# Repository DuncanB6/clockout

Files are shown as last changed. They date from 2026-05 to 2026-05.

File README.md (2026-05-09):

# Clockout

For years, analog clocks have been wasting time. Toiling away 24/7, they're only really appreciated for their hard work a few seconds a day when somebody is finally able to spare a brief glance. Sounds horribly inefficient? It is. Luckily, there's Clockout. Clockout is an analog clock that only updates to the current time when somebody looks at it. Now you may ask, is this really more energy efficient? Thanks to the near constant processing to look for people, no. But is it cheaper than a regular clock? Not at all, it uses over $100 in components. However, does it perform better than a regular clock? Definitely not, although it does do decently well. For all its weaknesses, it blows away its competition in only one field. It's slightly funny.

When a user walks into the room in front of the clock, an IR motion detector recognizes their movement. This is sent to a Raspberry Pi, and a blue LED illuminates to let the user know they're seen. The Pi then uses a Pi Camera to try and pick out a face. If this is successful, another indicator LED lights up before the hands adjust. The Pi pulls the real time (internet connected) and adjusts the hands to that time using a stepper motor connected to a gearbox. The entire system is powered off of a laptop power supply, which is stepped down to 5V for the Pi. 12V is pulled off this buck board for the stepper. 

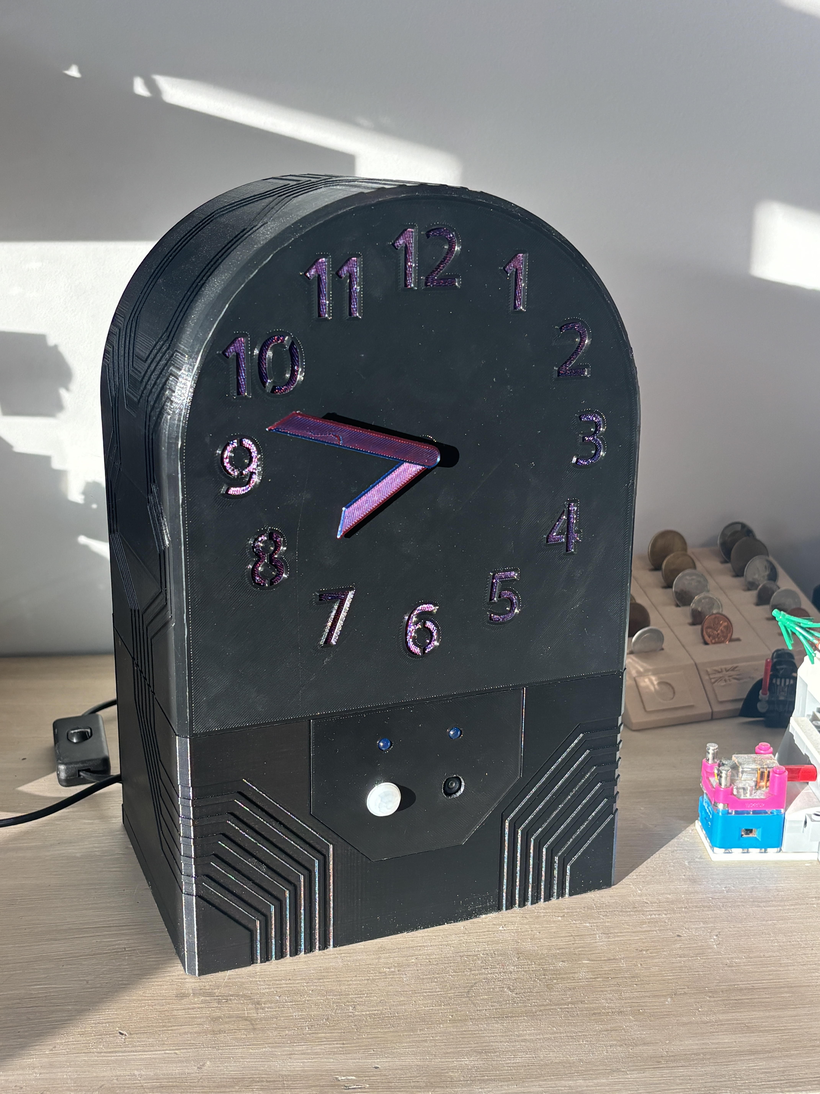
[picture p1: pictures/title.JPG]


This repository contains the software and hardware specs (STLs, BoM) that I used to make this project. Note that this is not a reproduction friendly project. You're welcome to use this idea, or even some of the resources here, but know that there are probably better options/designs out there.

## Software

Software for this project is a series of Python scripts. When running the primary script for full operation, functions from each script are used. Each individual script has a nameguarded section useful for testing it independantly.

### main.py

The main running file. This script handles all of the peripheral scripts, as well as handles the "state machine" and the hand adjustment math. 

#### Running the script
To run this script, use the following command:
"nohup python3 main.py 0630"

This runs the script indefinitely, even after disconnecting SSH. The argument (0630 in this case) should be the position of the clock hands when you run the script (6:30). See "calibrate.py" for positioning. To end the script, use the following two commands:
"ps aux | grep main.py"
"kill 4204"

Replace 4204 with the process ID discovered by the first command.

#### State machine

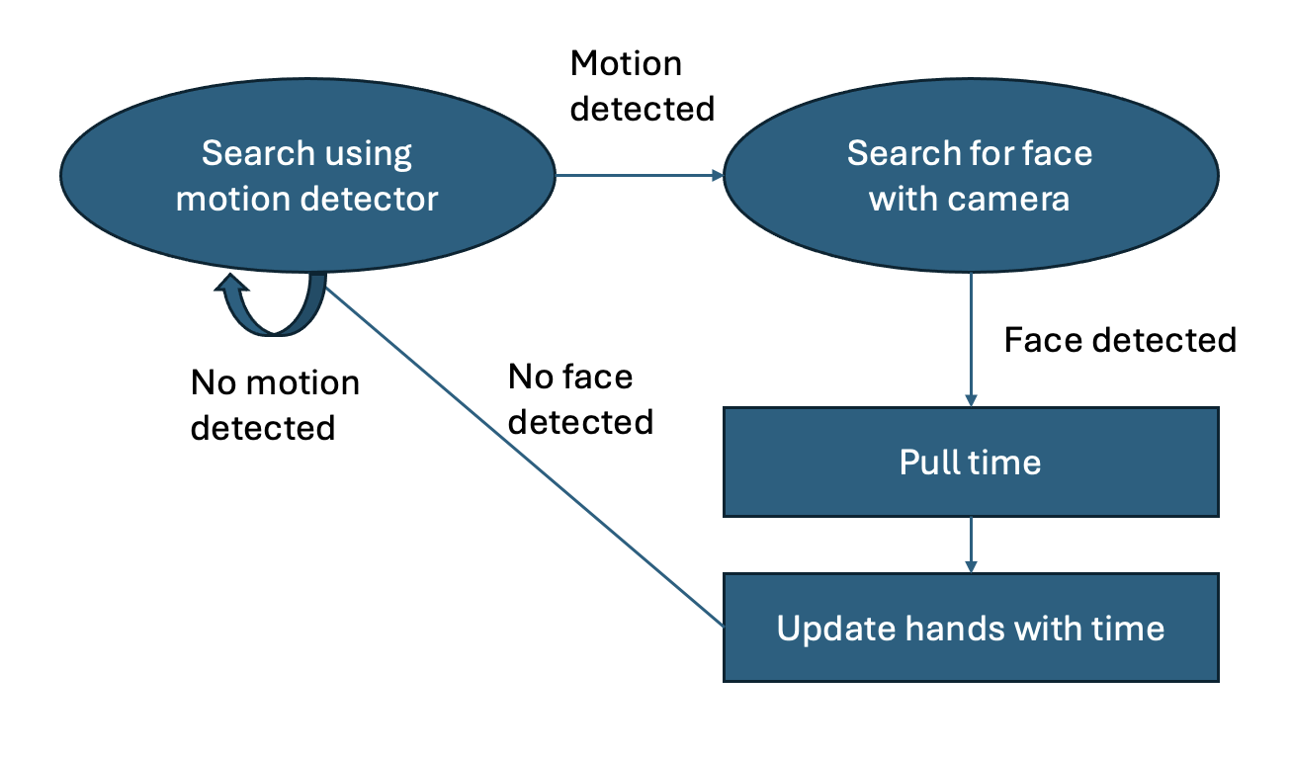
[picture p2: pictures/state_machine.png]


#### Clock hands math

This was one of the most technically challenging parts of the project surprisingly. It isn't all that complicated, but is hard to wrap your head around and hard to test (real time). This code finds the shortest distance in degrees between the current hands position and the desired position, then moves there.

### calibrate.py

This script allows the user to adjust the position of the hands. Enter a 4 digit number to exit. This is useful for testing, or if you'd like to line up the hands with a round time before starting for accuracy.

### camera.py

This script interacts with a Raspberry Pi PiCamera3 Wide Angle camera. It can take pictures, and detect faces in those pictures. Detection is done using a Haar cascade. A face is only registered when looking directly at the camera. Some tuning intructions are available in the comments. 

Watch out for the autofocus on this camera, if anything touches the lense area, it can mechanically block the autofocus, which causes problems for face detection.

### led.py

Dead simple script for toggling LEDs. Essentially a wrapper. 

### motion_detector.py

While this motion detector should probably be read using an ADC, it works pretty well as a digital read. This script simply takes that read.

### stepper.py

Controls the NEMA style stepper motor which spins the clock hands.

## Hardware

This section includes the component choices used in this project and the design of 3D printed components to house everything.

### BoM

See the BoM (excel sheet) in this repository. Note that the components used here are extremely overkill, and are still flawed. While I originally planned to use a Pi Zero 2W, the 4B offered easier development. The NEMA stepper is overkill in terms of power, and lacks any way of knowing its absolute position (a major flaw to this project). An ADC should really be used to read the motion detector, but digital worked fairly well, so I didn't. 

Many of the parts used were things I already had. I can't be bothered to go find out exactly what they are, you'll manage.

### Electronics Assembly

I avoided soldering to the Raspberry Pi, as it's quite expensive. Instead I used Arduino style jumpers, soldered to the other components with shrink wrap. For the stepper driver, I added a JST style connector. This allows me to more easily disconnect the top and bottom halves of the clock. 

All the electronics fit in quite poorly, largely because of long loose wires. The buck-Pi USB connection is especially troublesome, as the wire is stiff. Thankfully I had lots of space, and did lots of jamming.

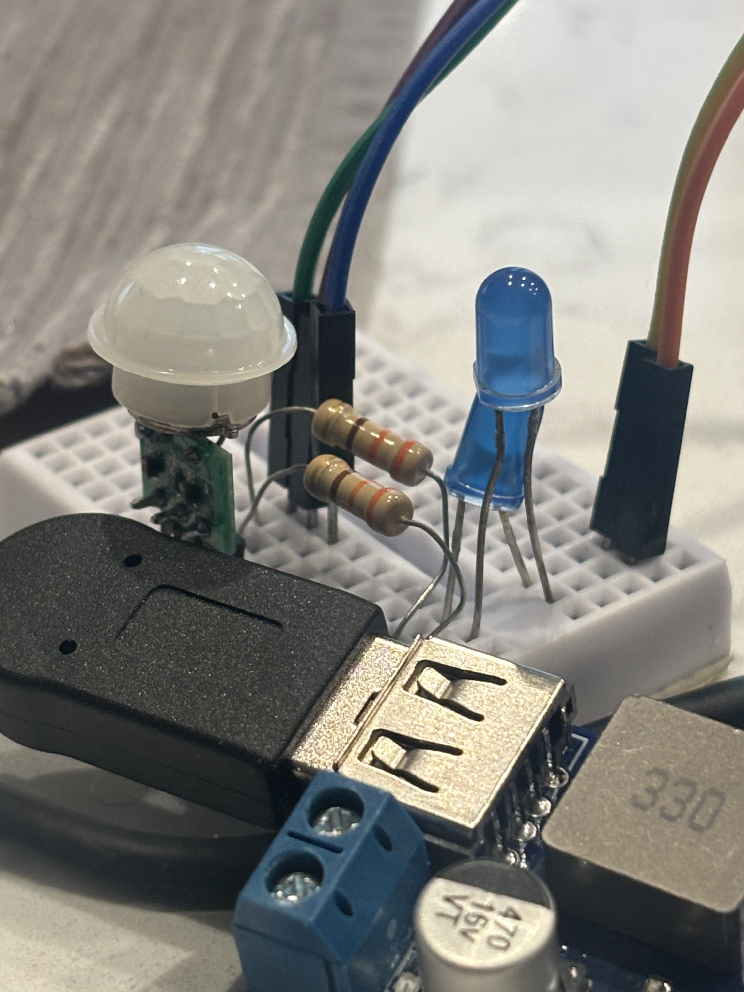
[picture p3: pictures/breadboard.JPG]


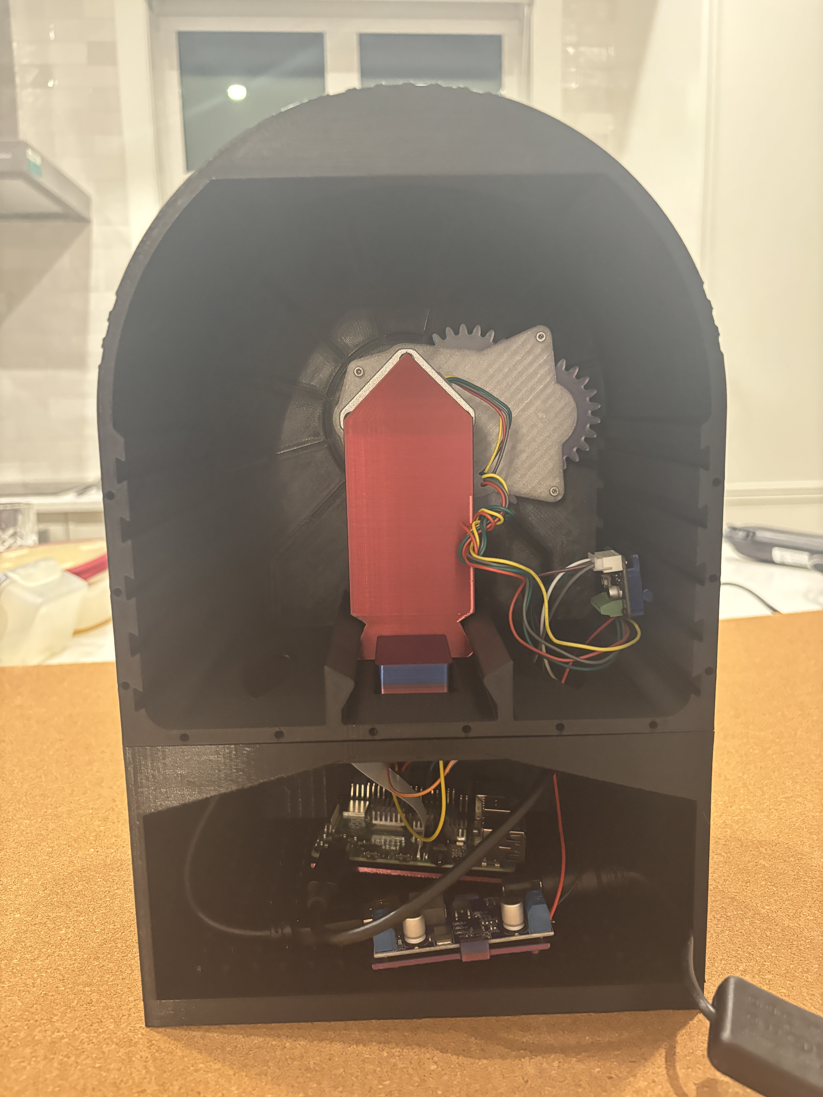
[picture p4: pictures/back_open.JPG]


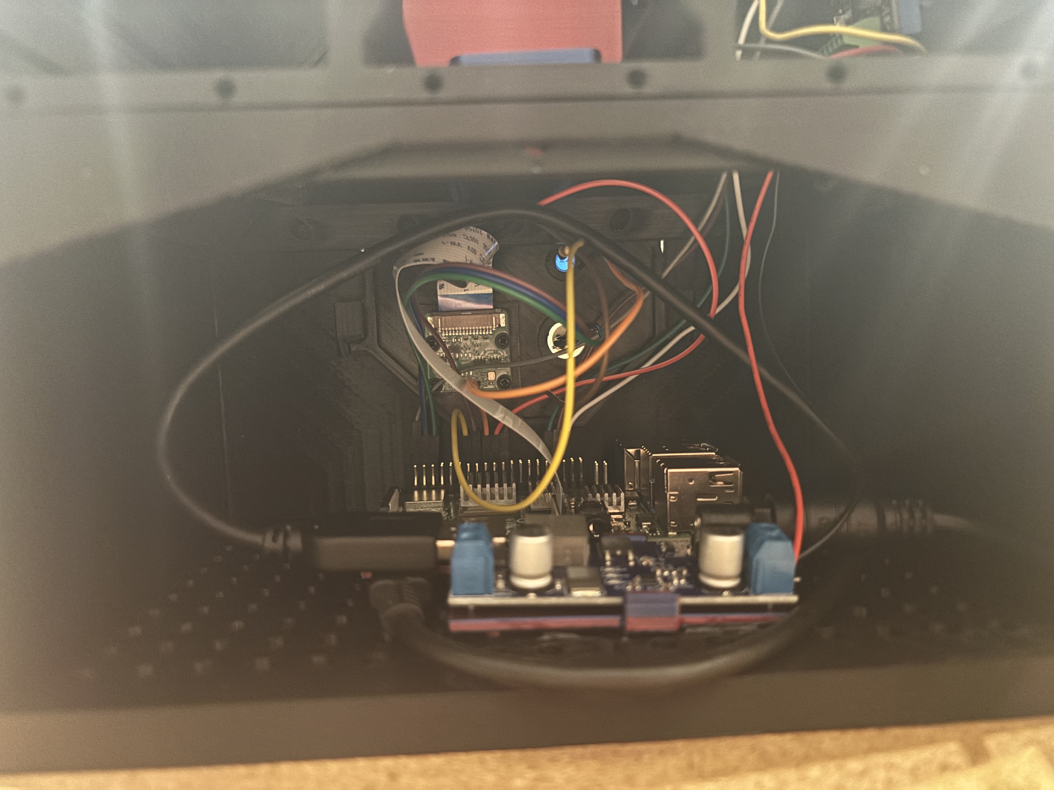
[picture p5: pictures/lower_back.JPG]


### 3D prints

All prints were done on a Prusa MK3S+ FDM printed. Almost all parts were printed in PLA, with the exception of the small gear on the stepper shaft which drives the gearbox. Since this is a high stress friction fit, PETG was used to prevent expansion over time. All files are available in the STLs folder. I make no claim to good designs. Some manual GCode editing was done to print the clock numbers in a different colour with two manual colour changes.

There was an attempt to make a nice modular system for mounting. This largely failed, as the parts weren't stiffly constrained enough for my jam-it-all-in assembly job.

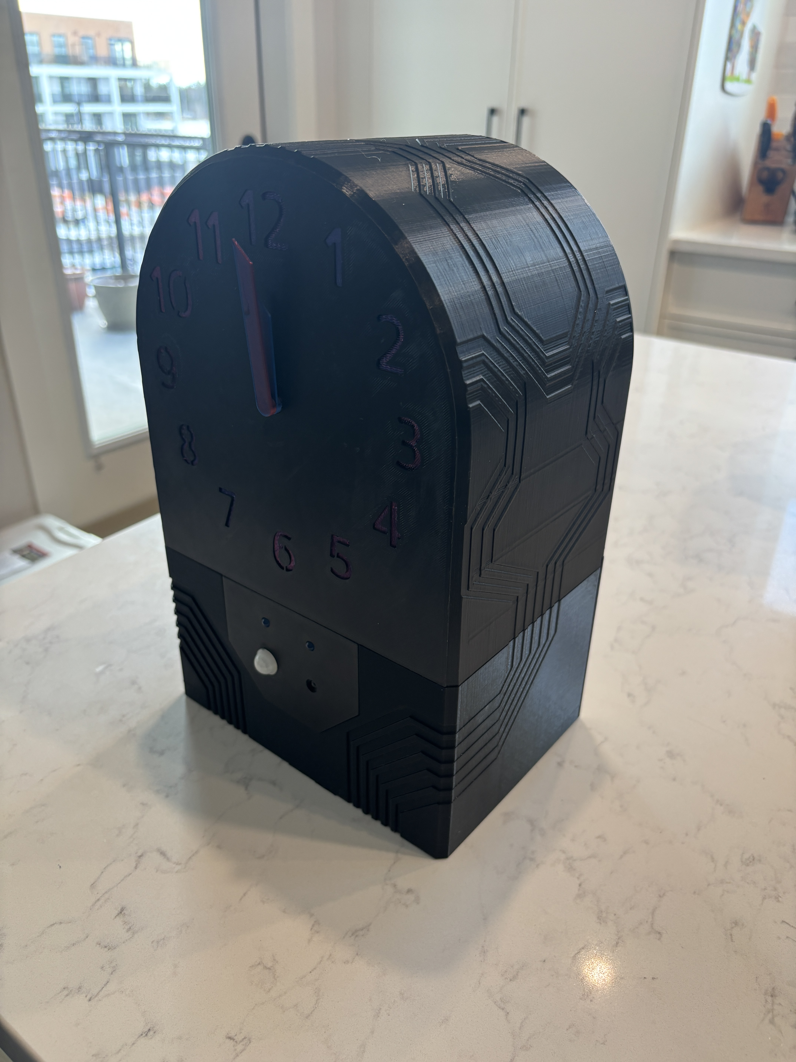
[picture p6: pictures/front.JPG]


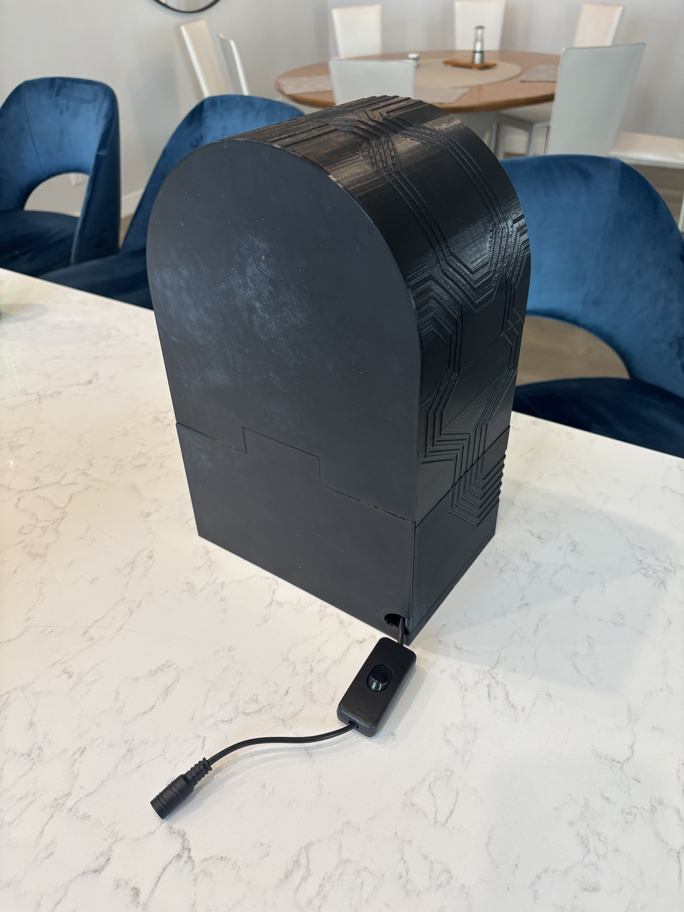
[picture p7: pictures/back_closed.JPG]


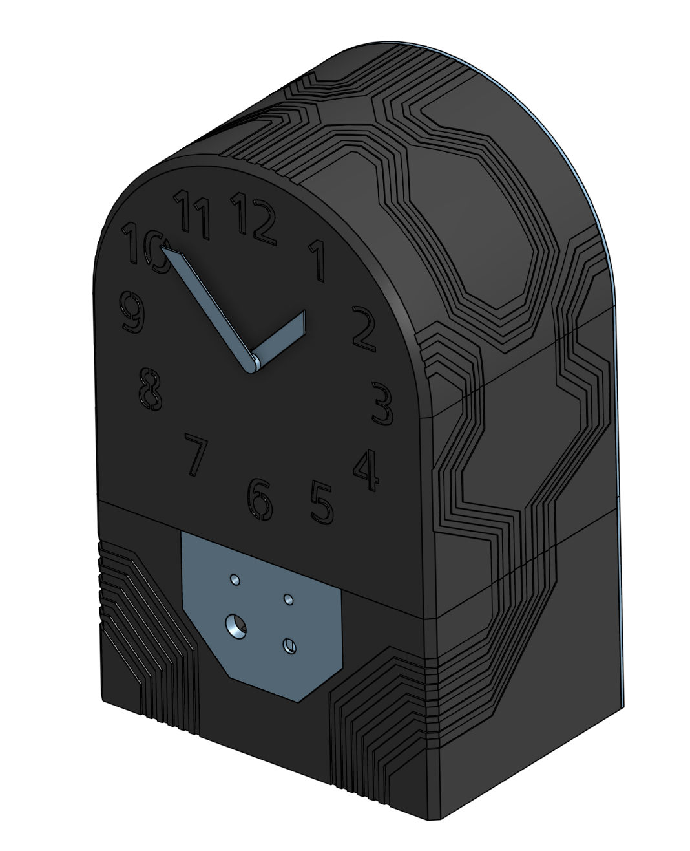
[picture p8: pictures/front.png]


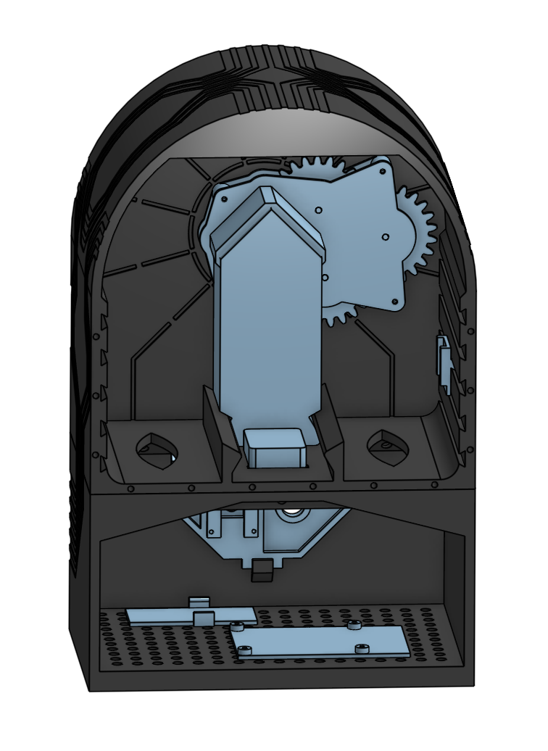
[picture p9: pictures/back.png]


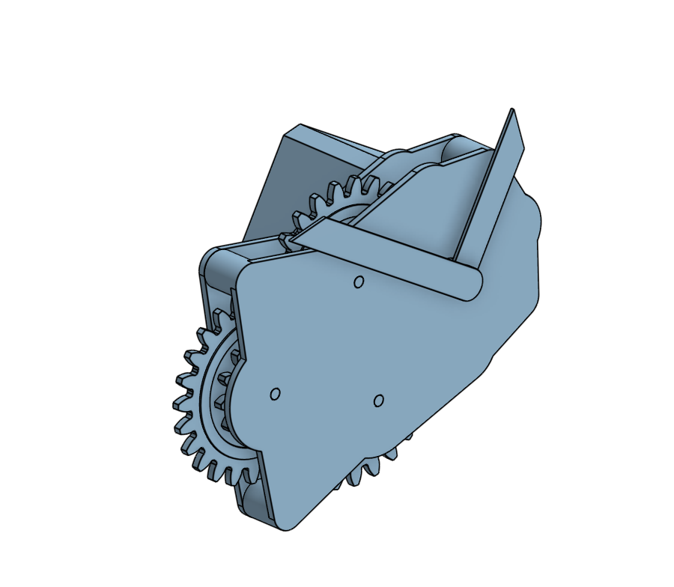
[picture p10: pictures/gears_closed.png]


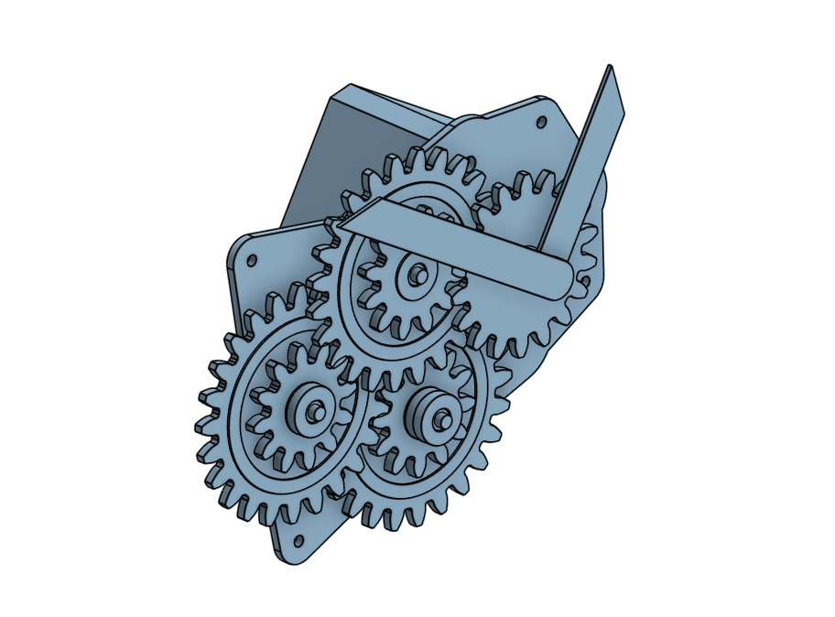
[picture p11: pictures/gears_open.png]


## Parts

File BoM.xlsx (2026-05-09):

Item | Used for | Cost (CAD) | Link | Notes
Raspberry Pi 4B | Main compute | - | - | I already had this
PLA | Clock body, component mounting, gearbox | - | - | I already had this
PETG | The gearbox drive gear | - | - | I already had this
DC-DC converter | Pi and stepper power | 3.99 | https://www.universal-solder.ca/product/dc-dc-converter-5v-5a-output-from-9-36v-input-screw-terminals-and-usb-output/
Power switch | Main power switch | 1.99 | https://www.universal-solder.ca/product/in-line-dc-power-switch-with-barrel-connector-2-1-5-5mm/
Motion sensor | Human detection | 3.99 | https://www.universal-solder.ca/product/pir-mini-motion-sensor-am312/
NEMA stepper | Clock hands control | 19.95 | https://www.pishop.ca/product/stepper-motor-nema-17-size-200-stepsrev-12v-350ma/?searchid=0&search_query=319
Stepper controller | Controlling stepper | 14.95 | https://www.pishop.ca/product/adafruit-tmc2209-stepper-motor-driver-breakout-board/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
Pi Camera | Detecting faces | 49 | https://www.pishop.ca/product/raspberry-pi-camera-module-3-wide/?searchid=0&search_query=527-1
12V power supply | Main power source | - | - | I already had this
Wires, solder, shrink wrap | Connecting components | - | - | I already had this
JST connector | Connect stepper control and Pi, allows seperation of 3D print halves | - | - | I already had this
Blue LEDs | Detection indicators | - | - | I already had this
USB cable | Connects buck board to Pi | - | - | I already had this

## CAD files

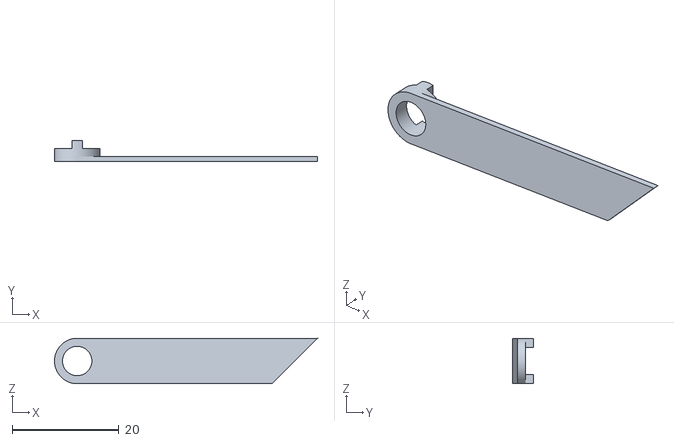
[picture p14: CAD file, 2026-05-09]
stls/clockout - Part 1 (11).stl
49.2 x 4.00 x 8.50

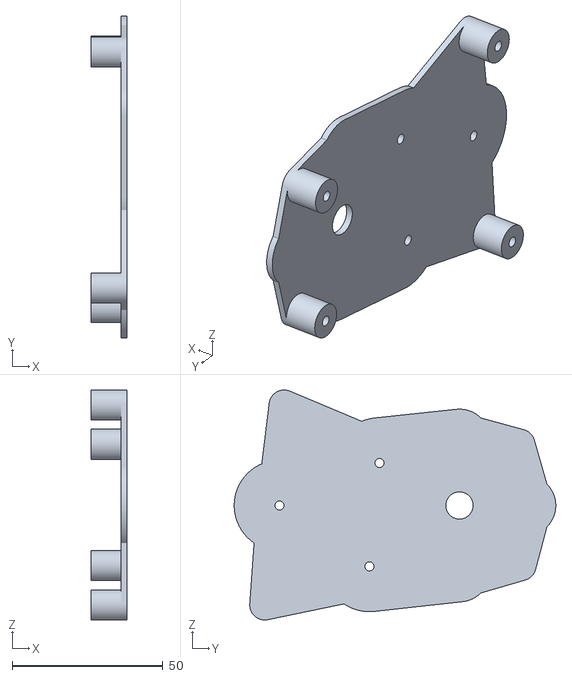
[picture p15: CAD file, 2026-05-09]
stls/clockout - Part 1 (14).stl
12.0 x 106.5 x 76.2

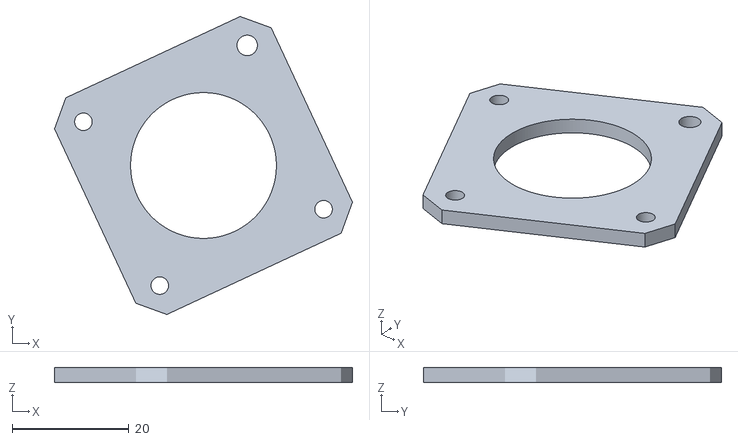
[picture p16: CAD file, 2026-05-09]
stls/clockout - Part 1 (10).stl
51.1 x 51.1 x 2.50

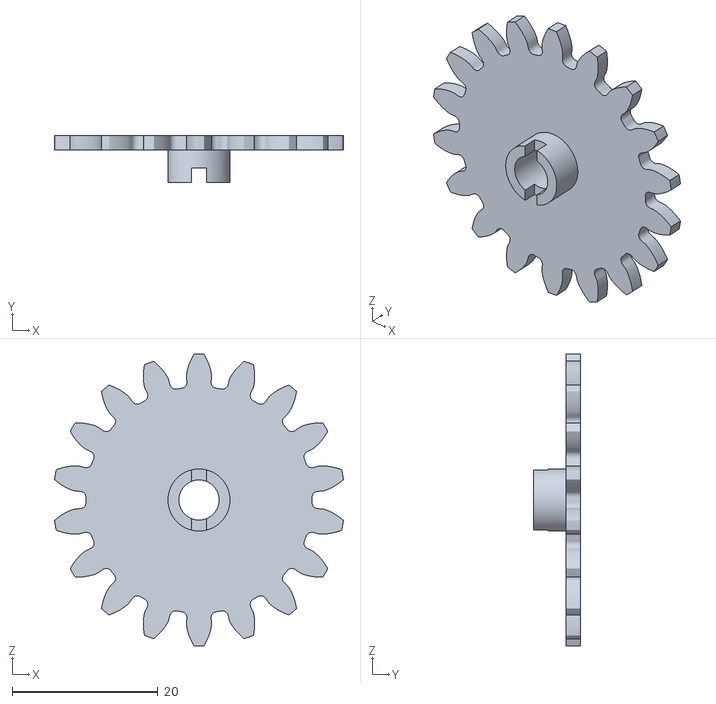
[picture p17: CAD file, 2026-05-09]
stls/clockout - Spur gear (18 teeth).stl
39.6 x 6.50 x 40.0

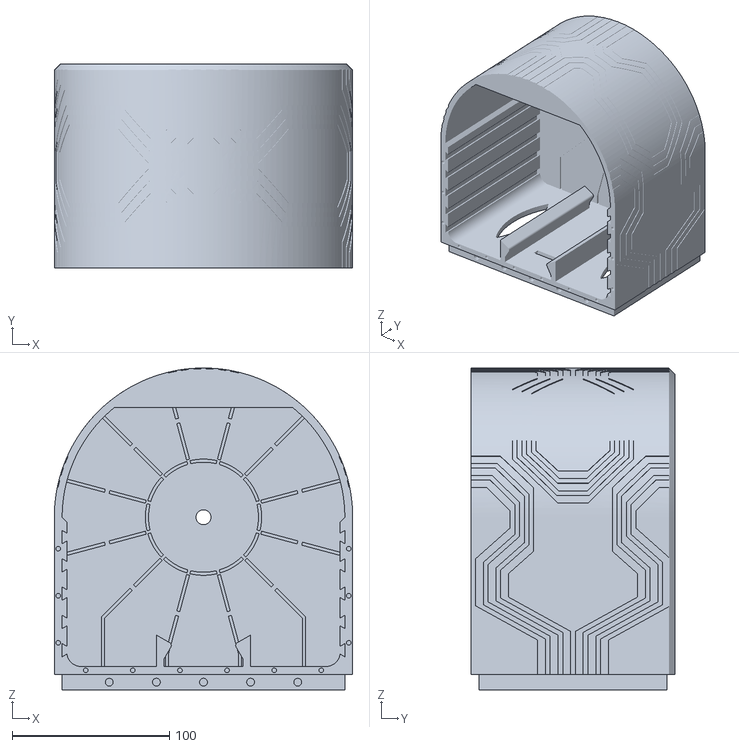
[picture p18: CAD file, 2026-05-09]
stls/clockout - Part 1 (16).stl
190.0 x 130.0 x 205.0

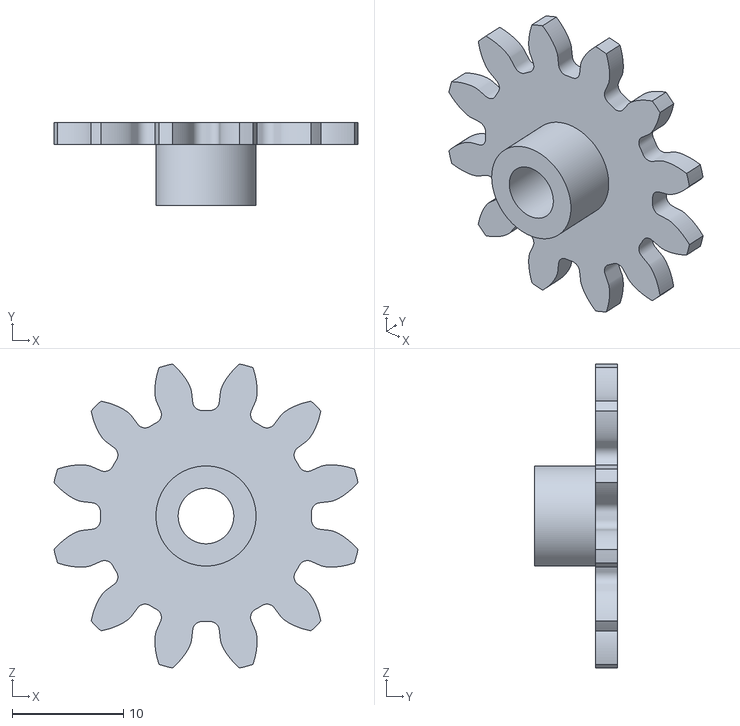
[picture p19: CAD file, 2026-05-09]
stls/clockout - Spur gear (12 teeth).stl
27.3 x 7.50 x 27.3

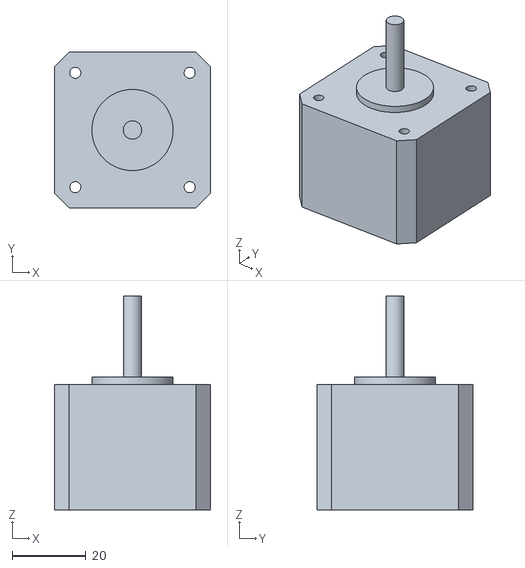
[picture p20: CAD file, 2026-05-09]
stls/clockout - Part 1 (17).stl
42.3 x 42.3 x 58.0

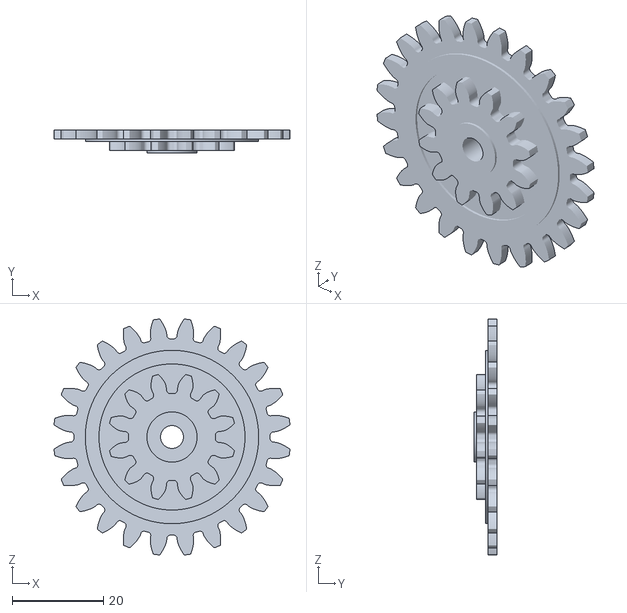
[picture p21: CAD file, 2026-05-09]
stls/clockout - Spur gear (24 teeth).stl
51.7 x 5.00 x 51.7

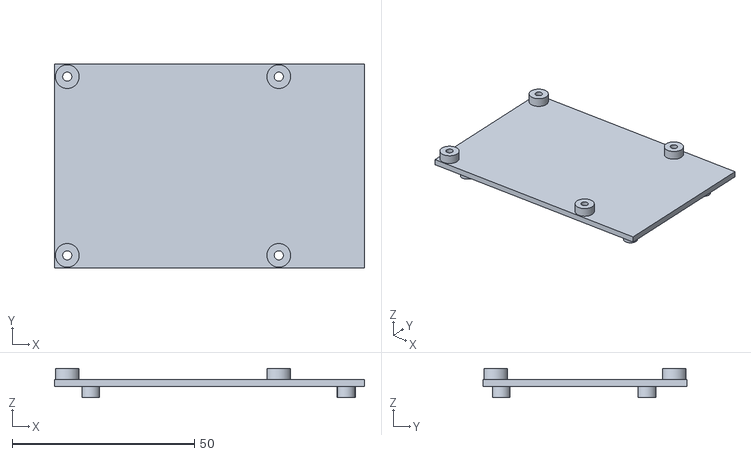
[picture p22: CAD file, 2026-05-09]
stls/clockout - Part 1.stl
85.0 x 56.0 x 8.00

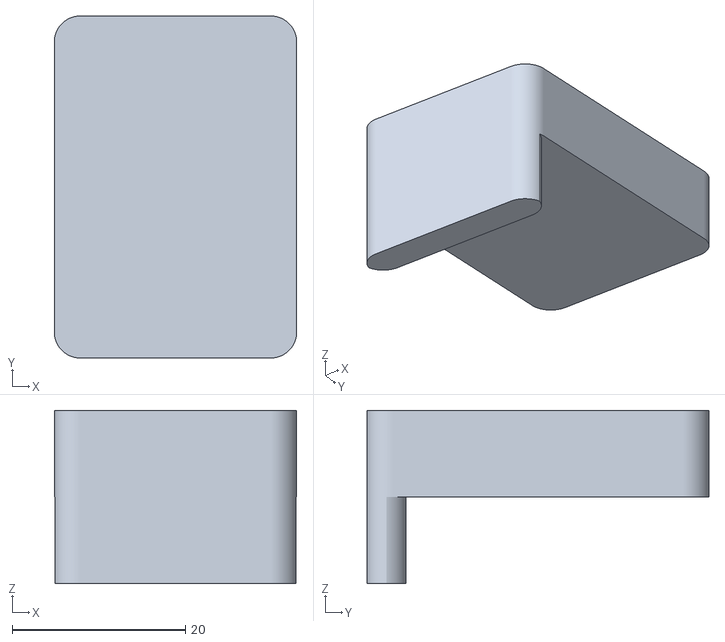
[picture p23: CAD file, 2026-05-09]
stls/clockout - Part 1 (15).stl
28.0 x 39.5 x 20.0

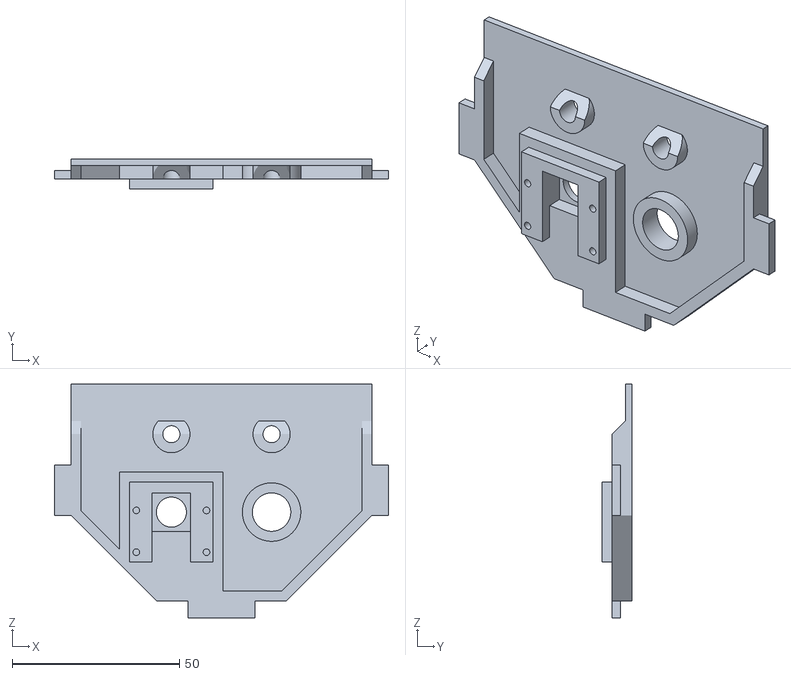
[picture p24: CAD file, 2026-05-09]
stls/clockout - Part 1 (12).stl
100.0 x 9.00 x 70.0

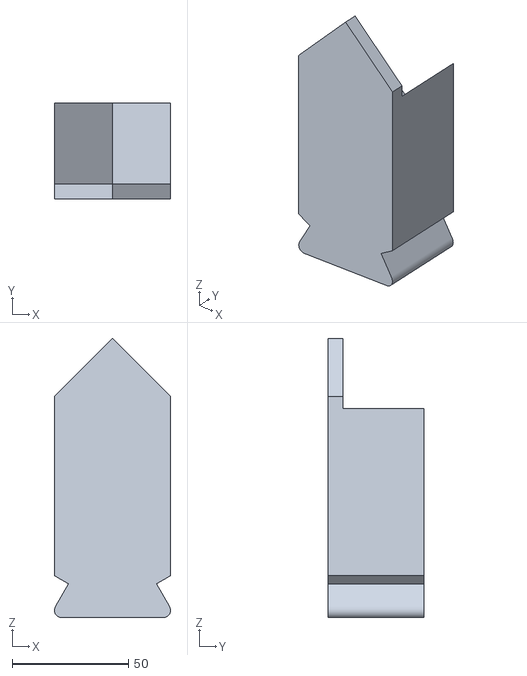
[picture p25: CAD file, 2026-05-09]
stls/clockout - Part 1 (13).stl
50.0 x 41.5 x 120.0

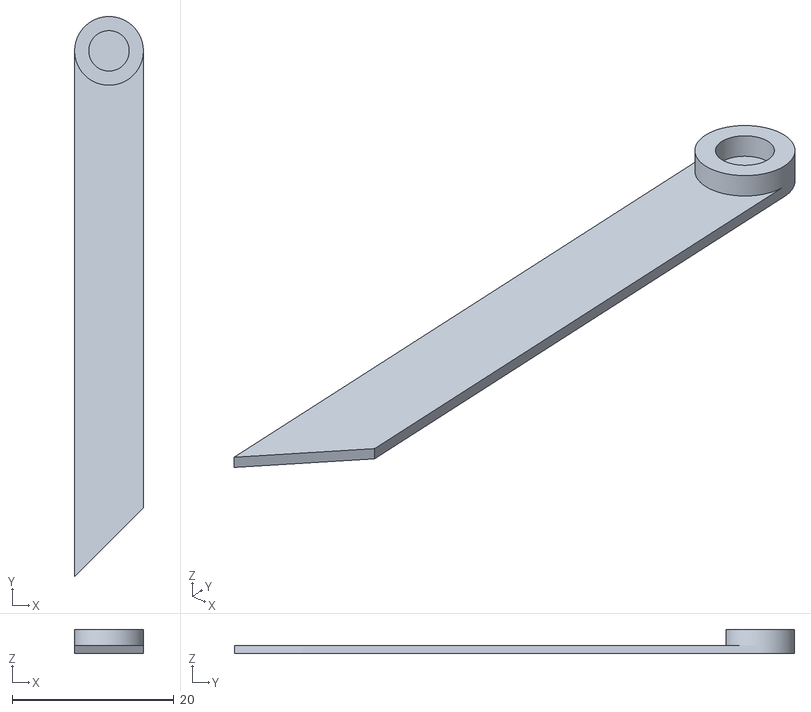
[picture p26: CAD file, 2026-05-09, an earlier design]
stls/clockout - Part 1 (9).stl
8.50 x 69.2 x 3.00

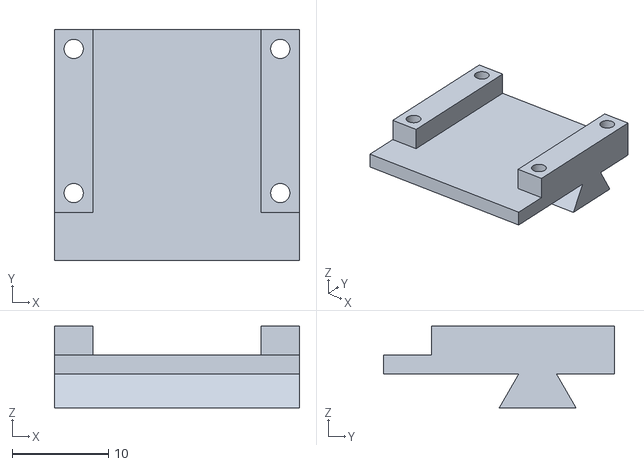
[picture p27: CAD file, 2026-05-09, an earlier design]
stls/clockout - Part 1 (8).stl
25.5 x 24.0 x 8.50

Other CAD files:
stls/clockout - Part 1 (4).stl
stls/clockout - Part 1 (7).stl
stls/clockout - Part 1 (6).stl
stls/clockout - Part 1 (3).stl
stls/clockout - Part 1 (1).stl
stls/clockout - Part 1 (2).stl
stls/clockout - Part 1 (5).stl

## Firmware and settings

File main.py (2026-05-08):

import RPi.GPIO as GPIO
from datetime import datetime
import time
import sys

from camera import Camera
from motion_detector import check_motion
from led import led_on, led_off
from stepper import spin_minute_degrees


MOTION_PIN = 23
MOTION_LED_PIN = 24
CAMERA_LED_PIN = 25
STEP_PIN = 16
DIR_PIN = 12


def setup():
    camera = Camera()

    GPIO.setmode(GPIO.BCM)

    GPIO.setup(MOTION_PIN, GPIO.IN, pull_up_down=GPIO.PUD_DOWN)
    GPIO.setup(MOTION_LED_PIN, GPIO.OUT)
    GPIO.setup(CAMERA_LED_PIN, GPIO.OUT)
    GPIO.setup(STEP_PIN, GPIO.OUT)
    GPIO.setup(DIR_PIN, GPIO.OUT)
    GPIO.setup(STEP_PIN, GPIO.OUT)

    return camera


def cleanup(camera):
    led_off(MOTION_LED_PIN)
    led_off(CAMERA_LED_PIN)

    camera.close_camera()

    GPIO.cleanup()

    return


def set_to_current_time(current_hands):
    current_hands = f"{current_hands:04d}"
    current_h = int(current_hands[:2]) % 12
    current_m = int(current_hands[2:])
    
    real_time = datetime.now()
    real_h = real_time.hour % 12
    real_m = real_time.minute

    print(f"It is {real_h}:{real_m}")

    current_angle = ((current_h * 360) + (current_m * 6)) % (12 * 360)
    real_angle = ((real_h * 360) + (real_m * 6)) % (12 * 360)

    diff = current_angle - real_angle
    if diff >= 0 and diff <= (6 * 360):
        spin_minute_degrees(diff, "counter_clockwise", "fast", STEP_PIN, DIR_PIN)
        current_hands = int(f"{real_h:02d}{real_m:02d}")
        print("Hands are now:", current_hands)
        return current_hands
    
    diff = real_angle - current_angle
    if diff >= 0 and diff <= (6 * 360):
        spin_minute_degrees(diff, "clockwise", "fast", STEP_PIN, DIR_PIN)
        current_hands = int(f"{real_h:02d}{real_m:02d}")
        print("Hands are now:", current_hands)
        return current_hands

    diff = 4320 - current_angle + real_angle
    if diff <= (6 * 360):
        spin_minute_degrees(diff, "clockwise", "fast", STEP_PIN, DIR_PIN)
        current_hands = int(f"{real_h:02d}{real_m:02d}")
        print("Hands are now:", current_hands)
        return current_hands

    diff = 4320 - real_angle + current_angle
    if diff <= (6 * 360):
        spin_minute_degrees(diff, "counter_clockwise", "fast", STEP_PIN, DIR_PIN)
        current_hands = int(f"{real_h:02d}{real_m:02d}")
        print("Hands are now:", current_hands)
        return current_hands
    
    else:
        raise ValueError(f"Current hands: {current_hands}\nCurrent angle: {current_angle}\n Real time: {real_time}\nReal angle: {real_angle}")

    return None


def wake_up():
    for ii in range(20):
        led_on(MOTION_LED_PIN)
        led_on(CAMERA_LED_PIN)
        time.sleep(1/(ii+3))
        led_off(MOTION_LED_PIN)
        led_off(CAMERA_LED_PIN)
        time.sleep(1/(ii+3))

    spin_minute_degrees(30, "counter_clockwise", "medium", STEP_PIN, DIR_PIN)
    spin_minute_degrees(30, "clockwise", "medium", STEP_PIN, DIR_PIN)
    spin_minute_degrees(30, "counter_clockwise", "medium", STEP_PIN, DIR_PIN)
    spin_minute_degrees(30, "clockwise", "medium", STEP_PIN, DIR_PIN)

    return


def main_loop(current_hands):
    camera = setup()

    wake_up()

    try:
        while True:
            led_off(MOTION_LED_PIN)
            led_off(CAMERA_LED_PIN)

            while check_motion(MOTION_PIN):
                
                led_on(MOTION_LED_PIN)

                camera.capture_image()
                face = camera.detect_face()

                led_off(CAMERA_LED_PIN)

                while face:

                    led_on(CAMERA_LED_PIN)

                    current_hands = set_to_current_time(current_hands)

                    camera.capture_image()
                    face = camera.detect_face()


    except KeyboardInterrupt:
        print("\nLoop interrupted by user. Exiting gracefully...")

    finally:
        cleanup(camera)

    return


if __name__ == "__main__":

    if len(sys.argv) < 2:
        print("Usage: python3 main.py <current_hands>")
        sys.exit(1)

    current_hands = int(sys.argv[1])

    print("Current hands input:", current_hands)

    main_loop(current_hands)
    

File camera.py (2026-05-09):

from picamera2 import Picamera2
import cv2
import time

class Camera:
    def __init__(self):
        self.image = None

        # use haarcascade_frontalface_alt_tree.xml for less sensitivity
        self.face_cascade_front = cv2.CascadeClassifier(cv2.data.haarcascades + 'haarcascade_frontalface_alt2.xml')

        self.camera = Picamera2()
        self.camera.configure(self.camera.create_still_configuration(main={"format": "RGB888"}))
        self.camera.start()

    def close_camera(self):
        self.camera.close()

    def capture_image(self):
        self.image = self.camera.capture_array()
        self.image = cv2.resize(self.image, (960, 540))
        self.image = cv2.cvtColor(self.image, cv2.COLOR_BGR2GRAY)
        self.image = cv2.rotate(self.image, cv2.ROTATE_180)

    def display_image(self, display_time):
        cv2.imshow("Captured Image", self.image)
        cv2.waitKey(1)
        time.sleep(display_time/1000)
        cv2.destroyAllWindows()

    def detect_face(self):
        
        # tuning:
        # - scaleFactor: how much is a region of the image enlarged between checks (higher -> faster, but more likely to miss faces)
        # - minNeighbours: how many filters need to hit in a region to confirm a face (higher -> fewer FPs, more FNs)
        # - minSize: min size of face (pixels) (lower detects faces farther away, more FPs)
        front_faces = self.face_cascade_front.detectMultiScale(self.image, scaleFactor=1.05, minNeighbors=10, minSize=(10, 10))
        
        # draw rectangle on face (debugging)
        # for (x, y, w, h) in front_faces:
        #     print("yo a face!")
        #     cv2.rectangle(self.image, (x, y), (x+w, y+h), (0, 255, 0), 2)

        if len(front_faces) > 0:
            return True
        else:
            return False


if __name__ == "__main__":
    camera = Camera()
    while (1):
        print("scanning...")
        camera.capture_image()
        camera.detect_face()
        camera.display_image(5000)
    
    camera.close_camera()

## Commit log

2025-09-28 reworked face id using haar filter, works with many FPs
2025-10-24 camera working on pi, basic capture
2025-10-30 camera taking photos on pi 4b
2025-10-30 camera functionality moved to object
2026-02-28 basic stepper functionality established
2026-02-28 deleted old camera script
2026-04-06 added LED control
2026-04-06 stepper modified for variable speed and direction
2026-04-08 minor fixes, added calibration
    [calibrate.py, main.py, stepper.py]
2026-05-01 may have fixed hands adjustment
    [camera.py, main.py]
2026-05-08 fixed hands adjustments (I hope)
    [camera.py, led.py, main.py]
2026-05-09 get documented idiot
    [BoM.xlsx, clockout - Part 1 (1).stl, clockout - Part 1 (10).stl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]
